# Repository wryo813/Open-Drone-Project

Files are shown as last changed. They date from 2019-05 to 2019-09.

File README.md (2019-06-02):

# Open Drone Project
## 概要
このプロジェクトは、Arduinoプラットフォーム上で開発可能なドローン制御システムの構築を目的としています。
***
# ハードウェア
## 電源仕様
### USBバスパワー給電時
- USB Type-C(USB2.0)で供給を行う
- バッテリーの充電が行われる
- バッテリー給電からUSBバスパワー給電に自動的に切り替わる
- システム全体の消費電流が750mAを超えるとリセッタブルヒューズの抵抗値が上がる
- ESP32-WROOM-32とバッテリー残量IC以外のセンサが起動する
- モーターが回転しないようソフト側で制限をかける
### バッテリー給電時
- 供給能力1000mA 3Cの[リチウムイオン二次電池](http://www.kyohritsu.jp/eclib/OTHER/DATASHEET/BATT/dtp603450phr.pdf)から供給を行う
- モーター含むシステム全体に電力を供給する
- すべての負荷はバッテリー残量ICを通過して電力が供給される
- 全モーターの消費電流が3A(仮)を超えたらソフト側で制限をかける
### バッテリー充電
- バッテリー充電はMCP73831-2ATI/OTを用いて行う
- 最大充電電流はPROG-GND間抵抗5kΩで最大200mAに設定する
#### MCP73831-2ATI/OTの最大充電電流の設定([公式データシート](https://www.microchip.jp/docs/DS21984B_JP.pdf)より)
```
IREG=最大充電電流
PROG=最大充電電流設定用抵抗

IREG=1000[V]/PROG[kΩ]
```
原則`最大充電電流[mA]≦バッテリー容量[mAh]`で設定する
### 消費電力
#### USBバスパワー給電時
|負荷 |消費電流 |
|---|---|
|[ESP32-WROOM-32D](https://www.espressif.com/sites/default/files/documentation/esp32-wroom-32_datasheet_en.pdf)|500mA|
|[MCP73831-2ATI/OT](https://www.microchip.jp/docs/DS21984B_JP.pdf)|200mA|
|[BQ27441-G1](http://www.tij.co.jp/jp/lit/ds/symlink/bq27441-g1.pdf)|0mA|
|[FT231XS](https://www.ftdichip.com/Support/Documents/DataSheets/ICs/DS_FT231X.pdf)|8mA|
|[BMX055](https://ae-bst.resource.bosch.com/media/_tech/media/datasheets/BST-BMX055-DS000.pdf)|8mA|
|[AE-VL53L0X](https://www.st.com/content/ccc/resource/technical/document/datasheet/group3/b2/1e/33/77/c6/92/47/6b/DM00279086/files/DM00279086.pdf/jcr:content/translations/en.DM002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)|19mA|
|[B0067](http://www.arducam.com/downloads/shields/ArduCAM_Mini_2MP_Camera_Shield_DS.pdf)|70mA|
|[モーター](http://www.vibration-motor.com/products/download/Q7AL2BX180003.pdf)|0mA|
|**合計**|805mA|
#### バッテリー給電時
|負荷 |消費電流 |
|---|---|
|[ESP32-WROOM-32D](https://www.espressif.com/sites/default/files/documentation/esp32-wroom-32_datasheet_en.pdf)|500mA|
|[MCP73831-2ATI/OT](https://www.microchip.jp/docs/DS21984B_JP.pdf)|0mA|
|[BQ27441-G1](http://www.tij.co.jp/jp/lit/ds/symlink/bq27441-g1.pdf)|0.097mA|
|[FT231XS](https://www.ftdichip.com/Support/Documents/DataSheets/ICs/DS_FT231X.pdf)|8mA|
|[BMX055](https://ae-bst.resource.bosch.com/media/_tech/media/datasheets/BST-BMX055-DS000.pdf)|8mA|
|[AE-VL53L0X](https://www.st.com/content/ccc/resource/technical/document/datasheet/group3/b2/1e/33/77/c6/92/47/6b/DM00279086/files/DM00279086.pdf/jcr:content/translations/en.DM002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)|19mA|
|[B0067](http://www.arducam.com/downloads/shields/ArduCAM_Mini_2MP_Camera_Shield_DS.pdf)|70mA|
|[モーター](http://www.vibration-motor.com/products/download/Q7AL2BX180003.pdf)|1130.4mA|
|**合計**|1739.097mA|
## 基板仕様
[回路図](https://twitter.com/w_ryo813/status/1123922796239781891)
[基板レイアウト](https://twitter.com/w_ryo813/status/1123887101588774915)
### 基板サイズ
- メイン基板 46×60mm
- 最外サイズ 95×95mm

# ソフトウェア
メインのプログラムは[Drone.ino](https://github.com/wryo813/Open-Drone-Project/blob/master/Drone.ino)
## 通信仕様
- 無線通信はWi-Fiを使って、送信機とドローン本体の一対一で行う
- 送信機とドローン本体は、両方ともAP+STAモードで相互に通信する
- 通信プロトコルはUDPを使用する
- Wi-Fi接続で使用するライブラリは[WiFi.h](https://www.arduino.cc/en/Reference/WiFi)
- UDP通信で使用するライブラリは[WiFiUdp.h](https://github.com/espressif/arduino-esp32/blob/master/libraries/WiFi/src/WiFiUdp.h)
### 送信機から送信するデータ
- 各モーターの目標角度
- YAW軸の目標角速度
- ドローン本体の目標高度
- 緊急停止信号
### ドローン本体から送信するデータ
- バッテリー残量
- 消費電力
- 残り飛行可能時間

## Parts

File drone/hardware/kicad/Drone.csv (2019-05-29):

ID | 参照記号 | パッケージ | 数 | 名称 | Supplier and ref
1 | U7 | Texas_S-PVSON-N10 | 1 | TPS63001
2 | U3 | BMX055 | 1 | BMX055
3 | J6 | JST_ACH_BM02B-ACHSS-GAN-ETF_1x02-1MP_P1.20mm_Vertical | 1 | Motor2
4 | J7 | JST_ACH_BM02B-ACHSS-GAN-ETF_1x02-1MP_P1.20mm_Vertical | 1 | Motor3
5 | J8 | JST_ACH_BM02B-ACHSS-GAN-ETF_1x02-1MP_P1.20mm_Vertical | 1 | Motor4
6 | J5 | JST_ACH_BM02B-ACHSS-GAN-ETF_1x02-1MP_P1.20mm_Vertical | 1 | Motor1
7 | J4 | JST_PH_S8B-PH-SM4-TB_1x08-1MP_P2.00mm_Horizontal | 1 | B0067
8 | J2 | JST_PH_S3B-PH-SM4-TB_1x03-1MP_P2.00mm_Horizontal | 1 | Battery
9 | SW1 | SW_SKRPACE010 | 1 | Power
10 | R41 | R_0603_1608Metric | 1 | 2.2M
11 | R45,R14,R15,R16,R18,R44 | R_0603_1608Metric | 6 | 5.1k
12 | REF**,REF**,REF**,REF** | motor | 4 | motor
13 | R34,R17,R19,R20,R21,R22,R23,R24,R25,R26,R27,R28,R29,R30,R31,R32,R35,R36,R37,R38,R46,R47,R48 | R_0603_1608Metric | 23 | 10k
14 | C1,C2 | C_0603_1608Metric | 2 | 47p
15 | C3 | C_0603_1608Metric | 1 | 0.01μ
16 | C4,C5,C6,C7,C8,C9,C10,C11,C12,C13,C14,C15,C29 | C_0603_1608Metric | 13 | 0.1μ
17 | C16 | C_0603_1608Metric | 1 | 0.47μ
18 | C19 | C_0603_1608Metric | 1 | 1μ
19 | C20,C21,C22 | C_0603_1608Metric | 3 | 4.7μ
20 | C23,C28,C30 | C_0603_1608Metric | 3 | 10μ
21 | C24,C25,C26,C27 | C_1210_3225Metric | 4 | 47μ
22 | D1,D3,D4,D5,D6 | D_SOD-123F | 5 | RB161MM-20
23 | D7 | LED_0603_1608Metric_Castellated | 1 | CHG
24 | D8 | LED_0603_1608Metric_Castellated | 1 | RX
25 | D9 | LED_0603_1608Metric_Castellated | 1 | TX
26 | D10 | LED_0603_1608Metric_Castellated | 1 | Power
27 | F1 | Fuse_1210_3225Metric | 1 | MICROSMD050F-2
28 | J1 | USB_C_Receptacle_Amphenol_12401610E4-2A | 1 | USB_C_Receptacle_USB2.0
29 | J3 | JST_S6B-ZR-SM4A-TF(LF)(SN) | 1 | AE-VL53L0X
30 | L1 | L_0805_2012Metric | 1 | BLM21PG331SN
31 | L2 | INDC2520X100 | 1 | LQM2HPN2R2MJH
32 | Q1,Q2 | SOT-23 | 2 | SS8050-G
33 | Q3,Q4 | SOT-23 | 2 | MMBT3904
34 | Q5 | SOT-23 | 1 | MMBT3906
35 | Q6,Q7,Q8,Q9 | SOT-23 | 4 | IRLML6344
36 | Q11 | SOT-23 | 1 | DMG3415U
37 | R1 | R_1206_3216Metric | 1 | 0.01Ω
38 | R2,R3 | R_0603_1608Metric | 2 | 22
39 | R4,R5,R6,R7,R33 | R_0603_1608Metric | 5 | 47
40 | R8 | R_0603_1608Metric | 1 | 100
41 | R9,R10 | R_0603_1608Metric | 2 | 470
42 | R11,R12,R13 | R_0603_1608Metric | 3 | 1k
43 | R39,R40 | R_0603_1608Metric | 2 | 1M
44 | R42,R43 | R_0603_1608Metric | 2 | 2.7k
45 | SW2 | SW_SKRPACE010 | 1 | EN
46 | SW3 | SW_SKRPACE010 | 1 | Boot
47 | U1 | ESP32-WROOM-32 | 1 | ESP32-WROOM-32D
48 | U2 | SSOP-20_3.9x8.7mm_P0.635mm | 1 | FT231XS
49 | U4 | Texas_S-PDSO-N12 | 1 | BQ27441-G1
50 | U6 | SOT-23-5 | 1 | MCP73831-2-OT

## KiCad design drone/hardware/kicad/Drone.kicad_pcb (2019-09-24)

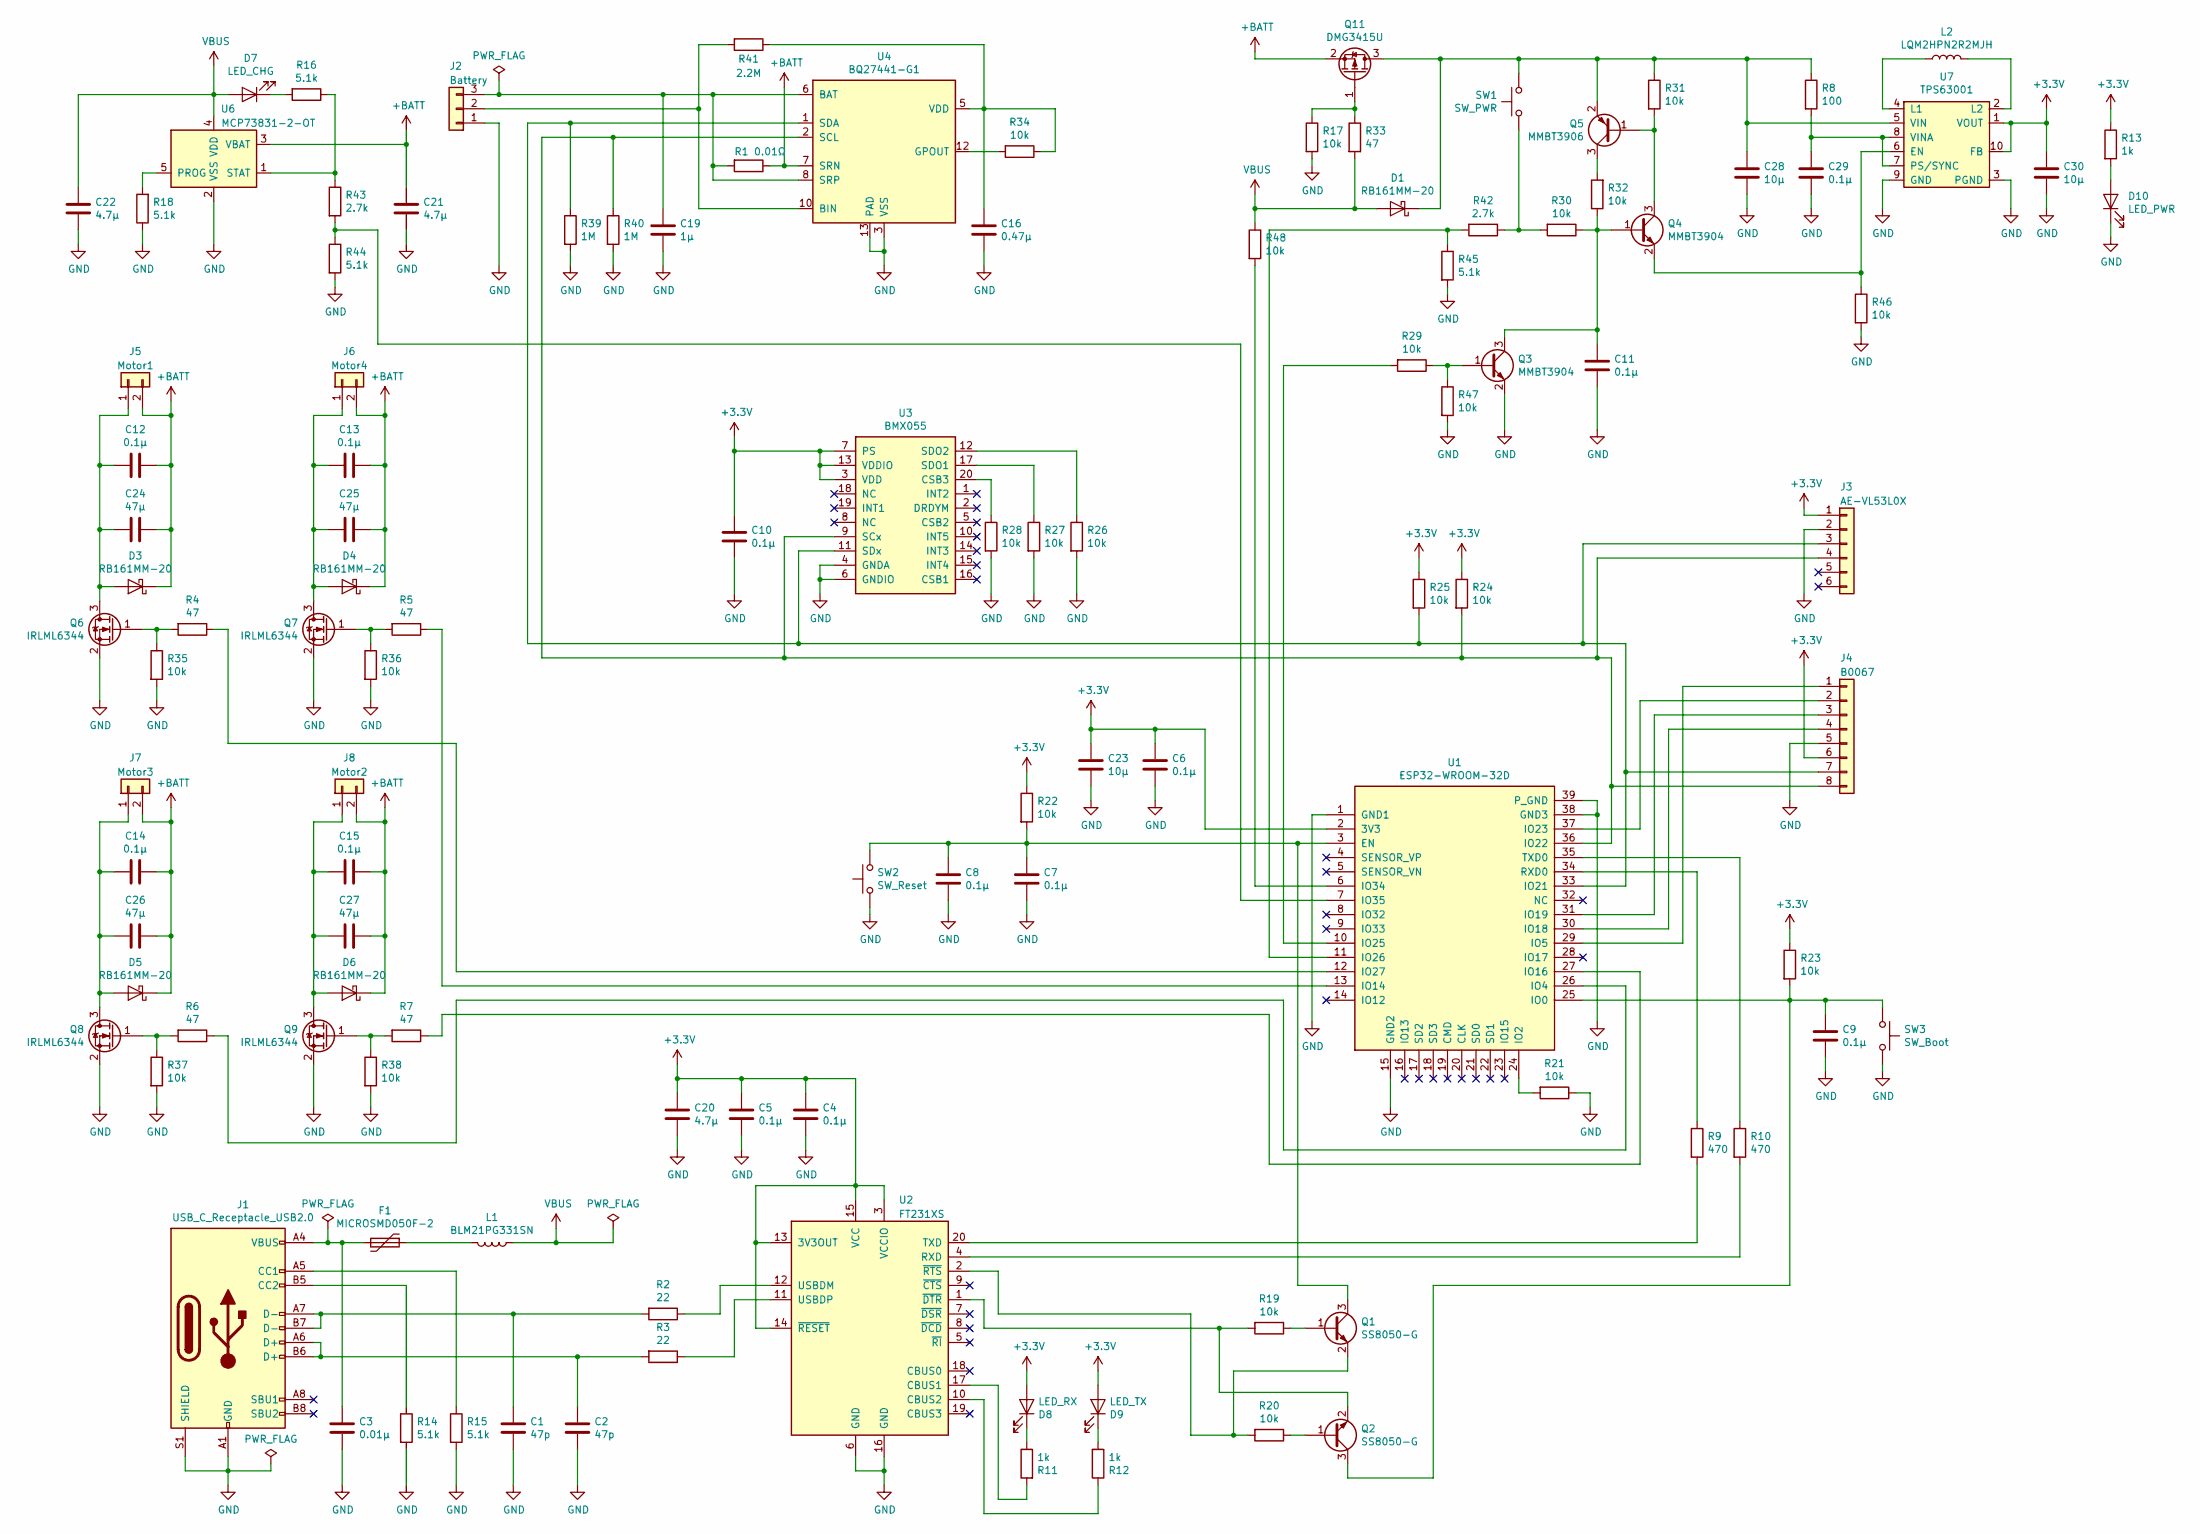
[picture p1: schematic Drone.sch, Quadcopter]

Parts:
C1, C2: 47p; C_0603_1608Metric
C3: 0.01μ; C_0603_1608Metric
C4, C5, C6, C7, C8, C9, C10, C11, C12, C13, C14, C15, C29: 0.1μ; C_0603_1608Metric
C16: 0.47μ; C_0603_1608Metric
C19: 1μ; C_0603_1608Metric
C20, C21, C22: 4.7μ; C_0603_1608Metric
C23, C28, C30: 10μ; C_0603_1608Metric
C24, C25, C26, C27: 47μ; C_1210_3225Metric
D1, D3, D4, D5, D6: RB161MM-20; D_SOD-123F
D7: LED_CHG; LED_0603_1608Metric_Castellated
D8: LED_RX; LED_0603_1608Metric_Castellated
D9: LED_TX; LED_0603_1608Metric_Castellated
D10: LED_PWR; LED_0603_1608Metric_Castellated
F1: MICROSMD050F-2; Fuse_1210_3225Metric
J1: USB_C_Receptacle_USB2.0; USB_C_Receptacle_Amphenol_12401610E4-2A
J2: Battery; JST_PH_S3B-PH-SM4-TB_1x03-1MP_P2.00mm_Horizontal
J3: AE-VL53L0X; JST_S6B-ZR-SM4A-TF(LF)(SN)
J4: B0067; JST_PH_S8B-PH-SM4-TB_1x08-1MP_P2.00mm_Horizontal
J5: Motor1; JST_SHL_SM02B-SHLS-TF_1x02-1MP_P1.00mm_Horizontal
J6: Motor4; JST_SHL_SM02B-SHLS-TF_1x02-1MP_P1.00mm_Horizontal
J7: Motor3; JST_SHL_SM02B-SHLS-TF_1x02-1MP_P1.00mm_Horizontal
J8: Motor2; JST_SHL_SM02B-SHLS-TF_1x02-1MP_P1.00mm_Horizontal
L1: BLM21PG331SN; L_0805_2012Metric
L2: LQM2HPN2R2MJH; INDC2520X100
Q1, Q2: SS8050-G; SOT-23
Q3, Q4: MMBT3904; SOT-23
Q5: MMBT3906; SOT-23
Q6, Q7, Q8, Q9: IRLML6344; SOT-23
Q11: DMG3415U; SOT-23
R1: 0.01Ω; R_1206_3216Metric
R2, R3: 22; R_0603_1608Metric
R4, R5, R6, R7, R33: 47; R_0603_1608Metric
R8: 100; R_0603_1608Metric
R9, R10: 470; R_0603_1608Metric
R11, R12, R13: 1k; R_0603_1608Metric
R14, R15, R16, R18, R44, R45: 5.1k; R_0603_1608Metric
R17, R19, R20, R21, R22, R23, R24, R25, R26, R27, R28, R29, R30, R31, R32, R34, R35, R36, R37, R38, R46, R47, R48: 10k; R_0603_1608Metric
R39, R40: 1M; R_0603_1608Metric
R41: 2.2M; R_0603_1608Metric
R42, R43: 2.7k; R_0603_1608Metric
SW1: SW_PWR; SW_SKRPACE010
SW2: SW_Reset; SW_SKRPACE010
SW3: SW_Boot; SW_SKRPACE010
U1: ESP32-WROOM-32D; ESP32-WROOM-32
U2: FT231XS; SSOP-20_3.9x8.7mm_P0.635mm
U3: BMX055; PQFN50P450X300X100-20N
U4: BQ27441-G1; Texas_S-PDSO-N12
U6: MCP73831-2-OT; SOT-23-5
U7: TPS63001; Texas_S-PVSON-N10

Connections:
+3V3: C4.1, C5.1, C6.1, C10.1, C20.1, C23.1, C30.1, D8.2 (A), D9.2 (A), J3.1, J4.6, R13.1, R22.1, R23.1, R24.1, R25.1, U1.2 (3V3), U2.3 (VCCIO), U2.13 (3V3OUT), U2.14 (~RESET), U2.15 (VCC), U3.3 (VDD), U3.7 (PS), U3.13 (VDDIO), U7.1 (VOUT), U7.10 (FB)
+BATT: C12.1, C13.1, C14.1, C15.1, C21.1, C24.1, C25.1, C26.1, C27.1, D3.1 (K), D4.1 (K), D5.1 (K), D6.1 (K), J5.2, J6.2, J7.2, J8.2, Q11.2 (S), R1.1, U4.7 (SRN), U6.3 (VBAT)
GND: C1.2, C2.2, C3.2, C4.2, C5.2, C6.2, C7.2, C8.2, C9.2, C10.2, C11.2, C16.2, C19.2, C20.2, C21.2, C22.2, C23.2, C28.2, C29.2, C30.2, D10.1 (K), J1.A1 (GND), J1.A12 (GND), J1.B1 (GND), J1.B12 (GND), J1.S1 (SHIELD), J2.1, J3.2, J4.5, Q3.2 (E), Q6.2 (S), Q7.2 (S), Q8.2 (S), Q9.2 (S), R14.2, R15.2, R17.2, R18.1, R21.1, R26.2, R27.2, R28.2, R35.2, R36.2, R37.2, R38.2, R39.2, R40.2, R44.2, R45.2, R46.2, R47.2, SW2.1, SW3.2, U1.1 (GND1), U1.15 (GND2), U1.38 (GND3), U1.39 (P_GND), U2.6 (GND), U2.16 (GND), U3.4 (GNDA), U3.6 (GNDIO), U4.3 (VSS), U4.13 (PAD), U6.2 (VSS), U7.3 (PGND), U7.9 (GND), U7.11
unnamed: C1.1, J1.A7 (D-), J1.B7 (D-), R2.2
unnamed: C2.1, J1.A6 (D+), J1.B6 (D+), R3.2
unnamed: C3.1, F1.2, J1.A4 (VBUS), J1.A9 (VBUS), J1.B4 (VBUS), J1.B9 (VBUS)
unnamed: C7.1, C8.1, Q1.3 (C), R22.2, SW2.2, U1.3 (EN)
unnamed: C9.1, Q2.3 (C), R23.2, SW3.1, U1.25 (IO0)
unnamed: C11.1, Q3.3 (C), Q4.1 (B), R30.1, R32.1
unnamed: C12.2, C24.2, D3.2 (A), J5.1, Q6.3 (D)
unnamed: C13.2, C25.2, D4.2 (A), J6.1, Q7.3 (D)
unnamed: C14.2, C26.2, D5.2 (A), J7.1, Q8.3 (D)
unnamed: C15.2, C27.2, D6.2 (A), J8.1, Q9.3 (D)
unnamed: C16.1, R34.1, R41.1, U4.5 (VDD)
unnamed: C19.1, J2.3, R1.2, U4.6 (BAT), U4.8 (SRP)
unnamed: C28.1, D1.1 (K), Q5.2 (E), Q11.3 (D), R8.1, R31.1, SW1.1, U7.5 (VIN)
unnamed: C29.1, R8.2, U7.7 (PS/SYNC), U7.8 (VINA)
unnamed: D7.1 (K), R16.2
unnamed: D8.1 (K), R11.1
unnamed: D9.1 (K), R12.2
unnamed: D10.2 (A), R13.2
unnamed: F1.1, L1.2
unnamed: J1.A5 (CC1), R15.1
unnamed: J1.B5 (CC2), R14.1
unnamed: J2.2, R41.2, U4.10 (BIN)
unnamed: J3.3, J4.7, R25.2, R39.1, U1.33 (IO21), U3.11 (SDx), U4.1 (SDA)
unnamed: J3.4, J4.8, R24.2, R40.1, U1.36 (IO22), U3.9 (SCx), U4.2 (SCL)
unnamed: J4.1, U1.29 (IO5)
unnamed: J4.2, U1.37 (IO23)
unnamed: J4.3, U1.31 (IO19)
unnamed: J4.4, U1.30 (IO18)
unnamed: L2.1, U7.4 (L1)
unnamed: L2.2, U7.2 (L2)
unnamed: Q1.1 (B), R19.1
unnamed: Q1.2 (E), R20.2, U2.2 (~RTS)
unnamed: Q2.1 (B), R20.1
unnamed: Q2.2 (E), R19.2, U2.1 (~DTR)
unnamed: Q3.1 (B), R29.1, R47.1
unnamed: Q4.2 (E), R46.1, U7.6 (EN)
unnamed: Q4.3 (C), Q5.1 (B), R31.2
unnamed: Q5.3 (C), R32.2
unnamed: Q6.1 (G), R4.2, R35.1
unnamed: Q7.1 (G), R5.2, R36.1
unnamed: Q8.1 (G), R6.2, R37.1
unnamed: Q9.1 (G), R7.2, R38.1
unnamed: Q11.1 (G), R17.1, R33.1
unnamed: R2.1, U2.12 (USBDM)
unnamed: R3.1, U2.11 (USBDP)
unnamed: R4.1, U1.12 (IO27)
unnamed: R5.1, U1.13 (IO14)
unnamed: R6.1, U1.26 (IO4)
unnamed: R7.1, U1.27 (IO16)
unnamed: R9.1, U1.34 (RXD0)
unnamed: R9.2, U2.20 (TXD)
unnamed: R10.1, U1.35 (TXD0)
unnamed: R10.2, U2.4 (RXD)
unnamed: R11.2, U2.17 (CBUS1)
unnamed: R12.1, U2.10 (CBUS2)
unnamed: R16.1, R43.1, U6.1 (STAT)
unnamed: R18.2, U6.5 (PROG)
unnamed: R21.2, U1.24 (IO2)
unnamed: R26.1, U3.12 (SDO2)
unnamed: R27.1, U3.17 (SDO1)
unnamed: R28.1, U3.20 (CSB3)
unnamed: R29.2, U1.10 (IO25)
unnamed: R30.2, R42.1, SW1.2
unnamed: R34.2, U4.12 (GPOUT)
unnamed: R42.2, R45.1, U1.11 (IO26)
unnamed: R43.2, R44.1, U1.7 (IO35)
unnamed: R48.2, U1.6 (IO34)
VBUS: C22.1, D1.2 (A), D7.2 (A), L1.1, R33.2, R48.1, U6.4 (VDD)

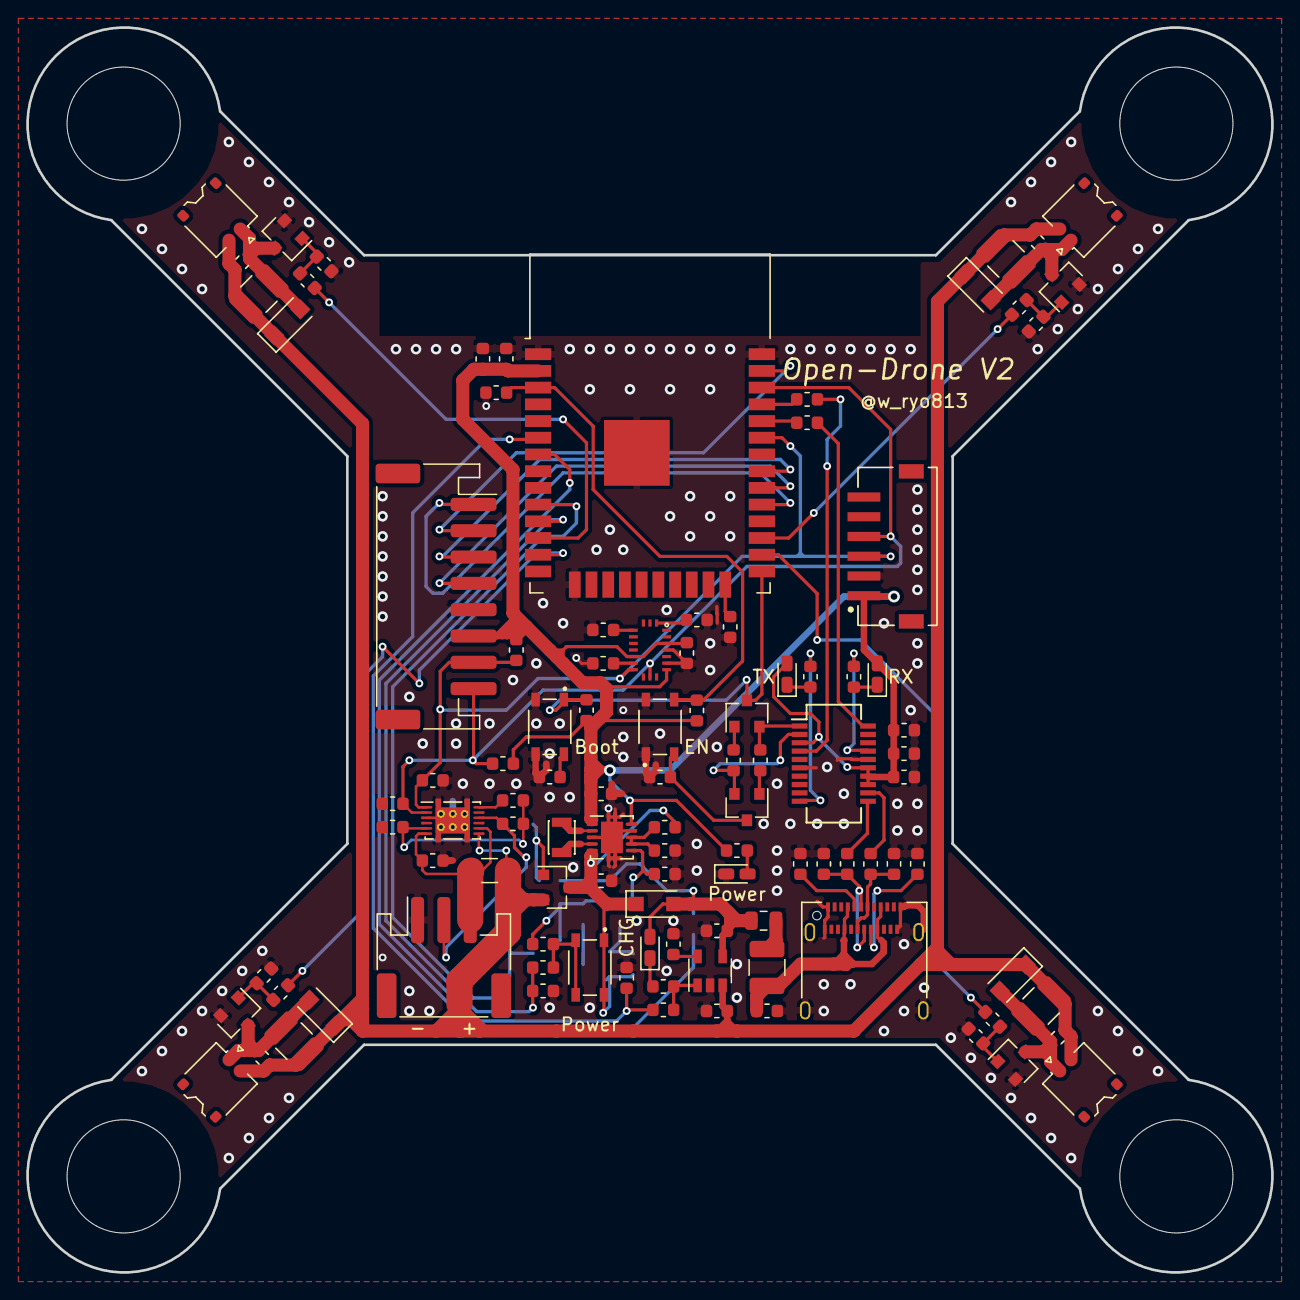
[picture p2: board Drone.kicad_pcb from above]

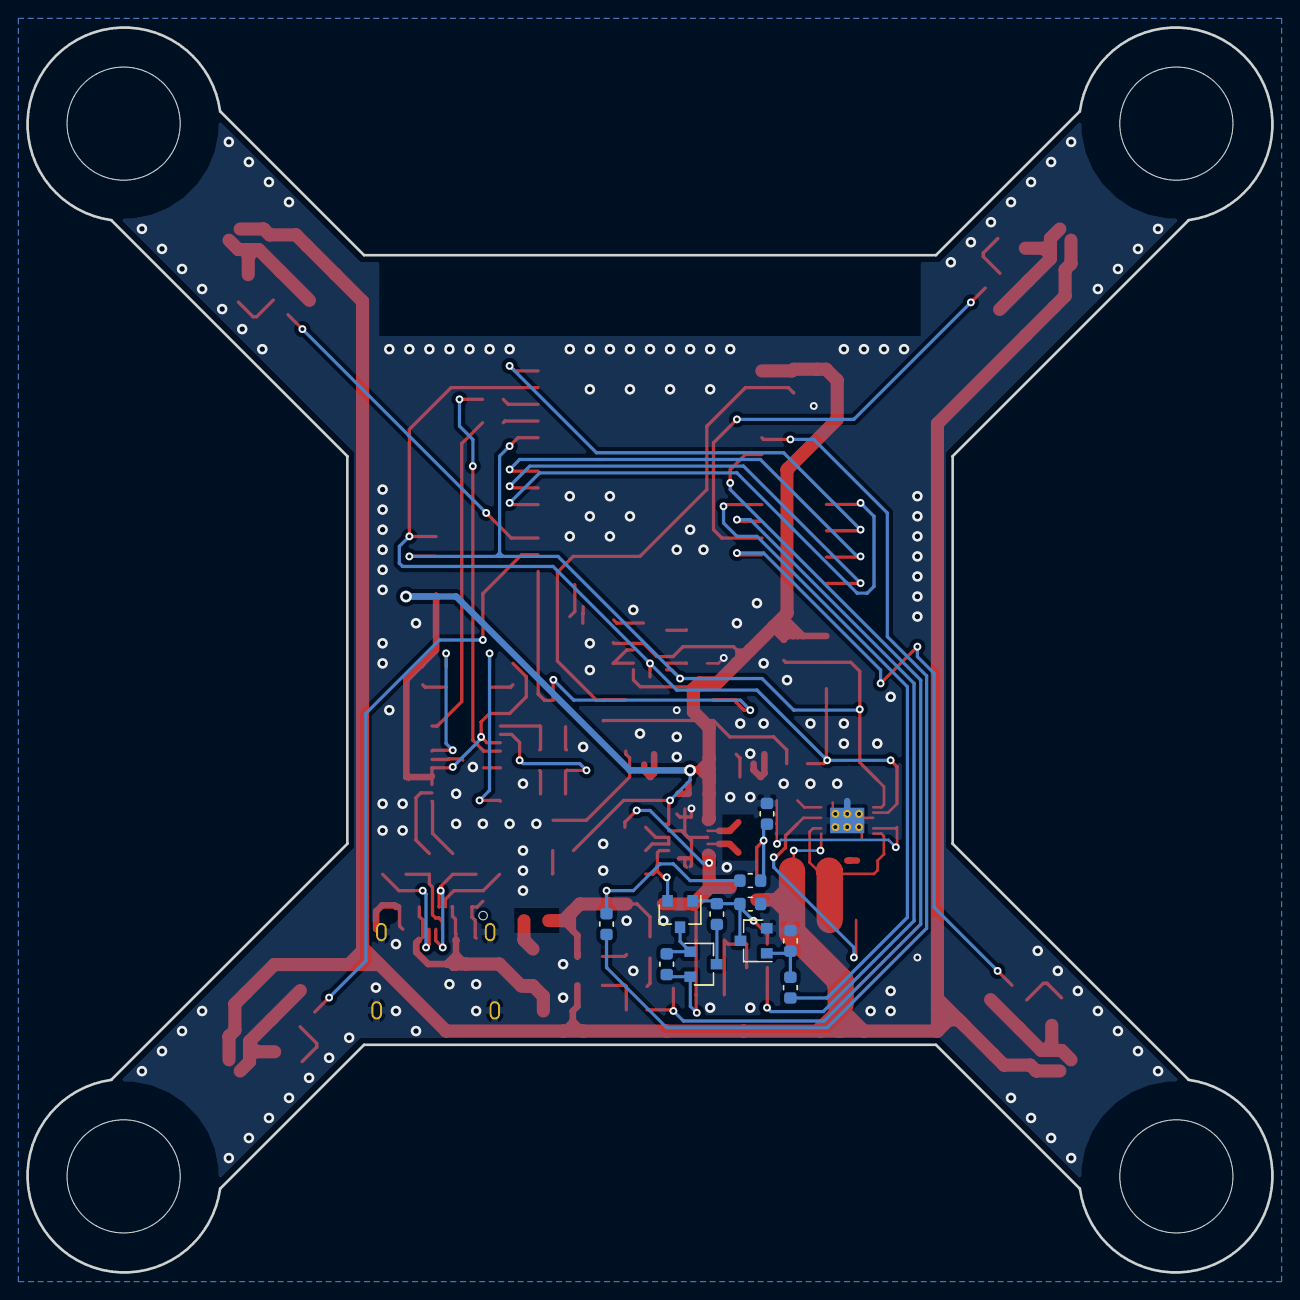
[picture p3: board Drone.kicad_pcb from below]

Board: 2 copper layers, 94.6 x 94.6 mm, 115 parts (11 on the bottom side), 71 nets.

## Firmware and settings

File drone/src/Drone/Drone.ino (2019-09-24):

/*
   メモ
   DTP603450を使ってモータを回転させると3Aでリミッターがかかって供給を停止する
   USB_STATUS_PINを使うとモーターからのノイズでモーターが一時的に停止することがある
   PW_SWITCH_PINを使うとモーターからのノイズで勝手にシャットダウンすることがある
   BQ27441が不安定

   TODO(優先順位)
   高度センサ

   完了
   オイラー角で姿勢角送信
   P_GAINの最適化
   PID制御の実装
   throttle_tgt_rawが0の時のみ電源スイッチを有効にする
   UDP通信で目標姿勢データと起動情報データの分解split関数を使う

   あきらめたこと
   バッテリーステータスの送信（IC割れた）
   電源スイッチ割込み
   カメラの実装
   DTP603450を使うこと
   USB使用時のモーター回転禁止

   PIDパラメータ最適値
   P制御
   P_GAIN=3.80

   PD制御
   P_GAIN=5.80
   D_GAIN=0.60

   PID制御
   P_GAIN 5.80
   I_GAIN 3.70
   D_GAIN 0.87
*/

#include <WiFi.h>
#include <WiFiUDP.h>
#include <MadgwickAHRS.h>
#include <SparkFunBQ27441.h>
#include "GPIO_config.h"
#include "BMX055.h"
#include "split.h"

//バッテリー容量[mAh]
#define BATTERY_CAPACITY 1000

//目標姿勢角度最大値[deg]
#define MAX_POSTURE_ANGLE 40
//目標yaw軸角速度最大値[deg/s]
#define MAX_YAW_VELOCITY 500
//スロットル最大値
#define MAX_THROTTLE 4095

//PIDパラメータ
#define P_GAIN 4.80
#define I_GAIN 2.70
#define D_GAIN 0.87

//yaw軸PIDパラメータ
#define YAW_P_GAIN 0
#define YAW_I_GAIN 0
#define YAW_D_GAIN 0

//重力加速度[m/s^2]
#define G_ACCL 9.80665

//受信する分割文字列数
#define STRING_NUM 6

//アクセスポイント設定 パスワードは8文字以上必要
const char* ssid     = "OpenDroneV2";
const char* password = "ODPpassword";

//自身のIPアドレス
IPAddress ip(192, 168, 4, 1);
//自身のゲートウェイ
IPAddress gateway(192, 168, 4, 1);
//自身のサブネットマスク
IPAddress subnet(255, 255, 255, 0);

//送信先のIPアドレス
static const char *remote_ip = "192.168.4.2";
//自身のUDPポート
static const int local_UDP_port = 8888;
//送信先のUDPポート
static const int rmote_UDP_port = 8889;

WiFiUDP udp;
Madgwick filter;
BMX055 IMU;

void setup() {
  //デバック用シリアル通信は115200bps
  Serial.begin(115200);
  Serial.println("Seial OK");

  //GPIO,PWMの初期化
  GPIO_setup();

  //バッテリー残量IC初期化
  lipo.begin();
  lipo.setCapacity(BATTERY_CAPACITY);
  Serial.println("battery OK");

  //モーションセンサ(BMX055)の初期化
  IMU.begin();
  Serial.println("IMU OK");

  //MadgwickFilterのサンプリンレート[Hz]
  //モーションセンサの出力データレート以下にする25Hz(MAX25Hz)
  filter.begin(25);

  //アクセスポイント構築
  WiFi.softAPConfig(ip, gateway, subnet);
  WiFi.softAP(ssid, password);
  Serial.print("SSID = ");
  Serial.println(ssid);
  Serial.print("Password = ");
  Serial.println(password);
  //機体のIPアドレスを表示
  IPAddress myIP = WiFi.softAPIP();
  Serial.print("AP IP address: ");
  Serial.println(myIP);
  Serial.println("Wi-Fi OK");

  //UDPサーバ構築
  udp.begin(local_UDP_port);
  Serial.println("UDP OK");

  Serial.print("P_GAIN = ");
  Serial.println(P_GAIN);
  Serial.print("I_GAIN = ");
  Serial.println(I_GAIN);
  Serial.print("D_GAIN = ");
  Serial.println(D_GAIN);

  Serial.println("Setting completed");
  delay(300);
}

void loop() {
  //スロットル目標値変数
  unsigned int throttle_tgt = 0;

  //デューティー比生値変数
  int motor1_duty_raw = 0;
  int motor2_duty_raw = 0;
  int motor3_duty_raw = 0;
  int motor4_duty_raw = 0;

  //モーションセンサへ姿勢データ取得リクエスト
  IMU.begin_Accl();
  IMU.begin_Gyro();
  IMU.begin_Mag();
  //モーションセンサから姿勢データを取得
  float gx = IMU.Gyro(x);
  float gy = IMU.Gyro(y);
  float gz = IMU.Gyro(z);
  //加速度センサの生値を重力加速度で割って[G]に変換
  float ax = IMU.Accl(x) / G_ACCL;
  float ay = IMU.Accl(y) / G_ACCL;
  float az = IMU.Accl(z) / G_ACCL;
  float mx = IMU.Mag(x);
  float my = IMU.Mag(y);
  float mz = IMU.Mag(z);

  //モーションセンサ生値をセンサーフュージョン
  filter.update(gx, gy, gz, ax, ay, az, mx, my, mz);
  //Madgwickフィルタで取得した姿勢角度を代入 0≦x＜360[deg]
  float roll  = filter.getRoll();
  float pitch = filter.getPitch();
  float yaw   = filter.getYaw();

  //UDP通信でパケットの存在を確認しサイズをpacketSizeに代入
  int packetSize = udp.parsePacket();
  //もしパケットを受信してたら
  if (packetSize > 0) {
    //UDP通信で受信した文字配列（文字列）を格納する配列
    char packetBuffer[255] = {0};
    //UDP通信での受信したサイズがpacketSizeの文字列をpacketBufferに代入し、受信した文字列の文字数をlenに代入。
    int len = udp.read(packetBuffer, packetSize);
    //分割した文字列を格納する配列をヌル文字で初期化
    String cmds[STRING_NUM] = {"\0"};
    //受信した文字列の最後にヌル文字を追加
    if (len > 0) packetBuffer[len] = '\0';

    //分割数 = 分割処理(文字列, 区切り文字, 配列)
    int index = split(packetBuffer, ',', cmds);
    //UDP到着データ種類判別・破損識別変数
    String data_type = cmds[0];
    //破損識別用最終データ変数
    String end_status = cmds[index - 1];
    //飛行データ取得成功
    if (data_type == "FLIGHT" && end_status == "END") {
      //取得した飛行データを変数に代入
      int roll_tgt_raw     = cmds[1].toInt();//-2047≦x≦2047
      int pitch_tgt_raw    = cmds[2].toInt();//-2047≦x≦2047
      int yaw_vel_tgt_raw  = cmds[3].toInt();//-2047≦x≦2047
      int throttle_tgt_raw = cmds[4].toInt();//0≦x≦4095

      //目標pitch軸角度,roll軸角度,yaw軸角速度の最大値を設定
      float roll_tgt    = (float)roll_tgt_raw    * MAX_POSTURE_ANGLE / 2047;
      float pitch_tgt   = (float)pitch_tgt_raw   * MAX_POSTURE_ANGLE / 2047;
      float yaw_vel_tgt = (float)yaw_vel_tgt_raw * MAX_YAW_VELOCITY  / 2047;
      //スロットル最大値を設定
      throttle_tgt      = throttle_tgt_raw       * MAX_THROTTLE      / 4095;

      //今回yaw軸角速度の算出に使う前回のyaw軸角度を格納する変数
      static float pre_yaw = 0;

      //モーター角度偏差の積分を格納する変数
      static float motor1_intg = 0;
      static float motor2_intg = 0;
      static float motor3_intg = 0;
      static float motor4_intg = 0;
      //yaw軸角速度偏差の積分を格納する変数
      static float yaw_vel_intg = 0;

      //前回のモーター角度偏差を格納する変数
      static float pre_motor1_devi = 0;
      static float pre_motor2_devi = 0;
      static float pre_motor3_devi = 0;
      static float pre_motor4_devi = 0;
      //前回のyaw軸角速度偏差を格納する変数
      static float pre_yaw_val_davi = 0;

      //ループ時間[s]
      float dt = loopTime();

      //yaw軸角速度[deg/s]
      float yaw_vel = (yaw - pre_yaw) / dt;
      //次回のyaw軸角速度算出に使う現在のyaw軸角度
      pre_yaw = yaw;
      //一回転したときに異常な値が出ないようにするための補正
      if (yaw_vel > 600) yaw_vel = yaw_vel - (360 / dt);
      else if (yaw_vel < -600) yaw_vel = yaw_vel + (360 / dt);

      //モーター角度偏差（目標モーター角度と現在のモーター角度の差）
      float motor1_devi = ( roll_tgt + pitch_tgt) - ( roll + pitch);
      float motor2_devi = ( roll_tgt - pitch_tgt) - ( roll - pitch);
      float motor3_devi = (-roll_tgt - pitch_tgt) - (-roll - pitch);
      float motor4_devi = (-roll_tgt + pitch_tgt) - (-roll + pitch);
      //yaw軸角速度偏差（目標yaw軸角速度と現在のyaw軸角速度の差）
      float yaw_vel_davi = yaw_vel_tgt - yaw_vel;

      //モーター角度偏差を時間で積分
      //モーター角度偏差とループ時間[s]をかけた値の累計を算出することで疑似的に積分している
      motor1_intg += motor1_devi * dt;
      motor2_intg += motor2_devi * dt;
      motor3_intg += motor3_devi * dt;
      motor4_intg += motor4_devi * dt;
      //yaw軸角速度偏差を時間で積分
      //yaw軸角速度偏差とループ時間[s]をかけた値の累計を算出することで疑似的に積分している
      yaw_vel_intg += yaw_vel_davi * dt;

      //モーターの暴走防止のため、スロットルが0の時はモーター角度偏差の積分とyaw軸角速度偏差の積分をリセット。
      if (throttle_tgt == 0) {
        motor1_intg = 0;
        motor2_intg = 0;
        motor3_intg = 0;
        motor4_intg = 0;
        yaw_vel_intg = 0;
      }

      //モーター角度偏差を時間で微分
      //モーター角度偏差の変化量をループ時間[s]で割ることで疑似的に微分している
      float motor1_diff = (motor1_devi - pre_motor1_devi) / dt;
      float motor2_diff = (motor2_devi - pre_motor2_devi) / dt;
      float motor3_diff = (motor3_devi - pre_motor3_devi) / dt;
      float motor4_diff = (motor4_devi - pre_motor4_devi) / dt;
      //次回のモーター角度偏差の微分に使う現在のモーター偏差
      pre_motor1_devi = motor1_devi;
      pre_motor2_devi = motor2_devi;
      pre_motor3_devi = motor3_devi;
      pre_motor4_devi = motor4_devi;
      //yaw軸角速度偏差を時間で微分
      //yaw軸角速度偏差の変化量をループ時間[s]で割ることで疑似的に微分している
      float yaw_vel_diff = (yaw_vel_davi - pre_yaw_val_davi) / dt;
      //次回のyaw軸角速度偏差の微分に使う現在のyaw軸角速度偏差
      pre_yaw_val_davi = yaw_vel_davi;

      //yaw軸角速度のPID制御
      float yaw_op = yaw_vel_davi * YAW_P_GAIN +  yaw_vel_intg * YAW_I_GAIN + yaw_vel_diff * YAW_D_GAIN;
      //モーター角度偏差のPID制御
      //yaw軸の制御のため、隣り合うモーターに異符号のyaw軸角速度偏差のPID制御を足す。
      motor1_duty_raw = throttle_tgt + motor1_devi * P_GAIN + motor1_intg * I_GAIN + motor1_diff * D_GAIN + yaw_op;
      motor2_duty_raw = throttle_tgt + motor2_devi * P_GAIN + motor2_intg * I_GAIN + motor2_diff * D_GAIN - yaw_op;
      motor3_duty_raw = throttle_tgt + motor3_devi * P_GAIN + motor3_intg * I_GAIN + motor3_diff * D_GAIN + yaw_op;
      motor4_duty_raw = throttle_tgt + motor4_devi * P_GAIN + motor4_intg * I_GAIN + motor4_diff * D_GAIN - yaw_op;

      //スロットルが0の時はモーターを回転させない
      if (throttle_tgt == 0) {
        motor1_duty_raw = 0;
        motor2_duty_raw = 0;
        motor3_duty_raw = 0;
        motor4_duty_raw = 0;
      }

      //UDP通信で送信するデータを生成
      String send_data  = "STATUS,";
      send_data += (String)millis() + ",";         //起動してからの経過時間
      send_data += (String)pitch_tgt + ",";        //目標pitch角度
      send_data += (String)pitch + ",";            //実測pitch角度
      send_data += (String)lipo.voltage() + ",";   //バッテリー電圧
      send_data += (String)lipo.current(AVG) + ",";//バッテリー電流
      send_data += (String)lipo.soc() + ",";       //バッテリー残量
      send_data += "END";

      //コントローラーにデータを送信
      udp.beginPacket(remote_ip, rmote_UDP_port);
      udp.print(send_data);
      udp.endPacket();
    }
  }

  //モーターのデューティー比を有効な範囲に収める
  motor1_duty_raw = constrain(motor1_duty_raw, 0, 4095);
  motor2_duty_raw = constrain(motor2_duty_raw, 0, 4095);
  motor3_duty_raw = constrain(motor3_duty_raw, 0, 4095);
  motor4_duty_raw = constrain(motor4_duty_raw, 0, 4095);

  //PWMを生成して出力
  //デューティー比は12bit 0≦x≦4095
  ledcWrite(0, motor1_duty_raw);
  ledcWrite(1, motor2_duty_raw);
  ledcWrite(2, motor3_duty_raw);
  ledcWrite(3, motor4_duty_raw);

  //目標スロットルが0かつ電源スイッチが押された時にshutdown_pw()を呼び出す
  if (throttle_tgt == 0 && digitalRead(PW_SWITCH_PIN) == HIGH) {
    shutdown_pw();
  }
}

//電源スイッチが押された時にシャットダウンする関数
void shutdown_pw() {
  //電源スイッチを押し続けている間はシャットダウンしない
  //これがないと、電源スイッチを押し続けている間起動とシャットダウンを繰り返す。
  while (digitalRead(PW_SWITCH_PIN) == HIGH);
  //シャットダウンピンをHIGHにする
  digitalWrite(SHUTDOWN_PIN, HIGH);
}

//ループ時間計測関数
//静的変数を使ってループ時間を計測しているので、二回以上呼び出すと正常に動作しない。
inline float loopTime() {
  float loop_time = 0;
  static float preTime = 0;

  //現在の時間から前回の時間を代入したpreTime引いたものを1000000で割って秒に変換
  loop_time = (micros() - preTime) / 1000000;
  //次の計測に使う現在の時間
  preTime = micros();

  return loop_time;
}

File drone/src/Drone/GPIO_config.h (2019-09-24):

#ifndef GPIO_config_h
#define GPIO_config_h

#include <Arduino.h>

//電源管理ピン設定
#define SHUTDOWN_PIN   25
#define PW_SWITCH_PIN  26
#define USB_STATUS_PIN 34
#define CHG_STATUS_PIN 35

//モーターピン設定
#define MOTOR1_PIN     27
#define MOTOR2_PIN     16
#define MOTOR3_PIN     4
#define MOTOR4_PIN     14

//PWM設定
/*
   PWM周波数とPWM分解能の設定
   T:周期[s],f:周波数[Hz],PWM_BIT:PWM分解能[bit],PWM_FREQ:PWM周波数[Hz] とする
   PWMのクロックタイマの周波数が80MHzの時、PWMのクロックタイマの周期は、
   T=1/f=1/(80×10^6)=12.5×10^(-9)s
   PWMのクロックタイマの周期とPWM分解能をかけた値の逆数がPWM周波数
   f=1/T=1/(12.5×10^(-9)×2^PWM_BIT[bit])=PWM_FREQ[Hz]
*/
//PWM周波数[Hz]
#define PWM_FREQ 19531
//PWM分解能[bit]
#define PWM_BIT 12

//GPIOの設定
void GPIO_setup(){
  //GPIO入出力設定
  //電源関連
  pinMode(PW_SWITCH_PIN, INPUT);
  pinMode(USB_STATUS_PIN, INPUT);
  pinMode(CHG_STATUS_PIN, INPUT);
  pinMode(SHUTDOWN_PIN, OUTPUT);
  //モーターピン
  pinMode(MOTOR1_PIN, OUTPUT);
  pinMode(MOTOR2_PIN, OUTPUT);
  pinMode(MOTOR3_PIN, OUTPUT);
  pinMode(MOTOR4_PIN, OUTPUT);
  //未使用ピン
  pinMode(13, INPUT_PULLUP);
  pinMode(17, INPUT_PULLUP);
  pinMode(32, INPUT_PULLUP);
  pinMode(33, INPUT_PULLUP);

  //モーターピンの初期化
  digitalWrite(MOTOR1_PIN, LOW);
  digitalWrite(MOTOR2_PIN, LOW);
  digitalWrite(MOTOR3_PIN, LOW);
  digitalWrite(MOTOR4_PIN, LOW);

  //PWM設定
  ledcSetup(0, PWM_FREQ, PWM_BIT);
  ledcSetup(1, PWM_FREQ, PWM_BIT);
  ledcSetup(2, PWM_FREQ, PWM_BIT);
  ledcSetup(3, PWM_FREQ, PWM_BIT);

  //ピンをチャンネルに接続
  ledcAttachPin(MOTOR1_PIN, 0);
  ledcAttachPin(MOTOR2_PIN, 1);
  ledcAttachPin(MOTOR3_PIN, 2);
  ledcAttachPin(MOTOR4_PIN, 3);

  Serial.println("GPIO OK");
}

#endif

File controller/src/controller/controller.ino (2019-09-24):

#include <WiFi.h>
#include <WiFiUDP.h>
#include "GPIO_config.h"
#include "split.h"

//ジョイスティックの初期状態の平均値を求める際のジョイスティック電圧読み込み回数
#define AVG_CNT 100

//受信する分割文字列数
#define STRING_NUM 8

//接続先アクセスポイントのSSID/パスワード
const char ssid[] = "OpenDroneV2"; // SSID
const char pass[] = "ODPpassword"; // password

//自身のIPアドレス
IPAddress ip(192, 168, 4, 2);
//自身のゲートウェイ
IPAddress gateway(192, 168, 4, 1);
//自身のサブネットマスク
IPAddress subnet(255, 255, 255, 0);
//自身のDNSサーバ
IPAddress DNS(192, 168, 4, 1);

//送信先のIPアドレス
static const char *remote_ip    = "192.168.4.1";
//自身のUDPポート
static const int local_UDP_port = 8889;
//送信先のUDPポート
static const int rmote_UDP_port = 8888;

//初期状態のジョイスティックの値を格納する変数
int rxv_pro = 0;
int ryv_pro = 0;
int lxv_pro = 0;
int lyv_pro = 0;

WiFiUDP udp;

void setup() {
  //デバック用シリアル通信は115200bps
  Serial.begin(115200);
  
  //GPIOの初期化
  GPIO_setup();
  Serial.println("GPIO OK");
  
  //初期状態のジョイスティックの値を取得
  joystick_proofread();
  Serial.println("Joystick OK");

  //自身のIPアドレス、ゲートウェイ、サブネットマスク、DNSサーバの設定
  WiFi.config(ip, gateway, subnet, DNS);
  //アクセスポイントに設定した機体にWi-Fi接続
  WiFi.begin(ssid, pass);
  Serial.println("weiting");
  //接続されるまで待機
  while (WiFi.status() != WL_CONNECTED);
  Serial.println("conected");
  
  //UDPサーバ構築
  udp.begin(local_UDP_port);
  Serial.println("UDP OK");

  Serial.println("Setting completed");
  delay(300);
}

void loop() {
  //Wi-Fiが切断された時に再接続を開始
  if (WiFi.status() != WL_CONNECTED) {
    //完全にWi-Fiを切断
    WiFi.disconnect();
    delay(50);
    //アクセスポイントに再接続
    WiFi.begin(ssid, pass);
  }
  
  //初期状態のジョイスティックの値を引くことで、ジョイスティックが中心の時に0になる。
  int lxv = analogRead(JOYSTICK_LX_PIN) - lxv_pro;//-2047≦x≦2047
  int lyv = analogRead(JOYSTICK_LY_PIN) - lyv_pro;//0≦x≦4095
  int rxv = analogRead(JOYSTICK_RX_PIN) - rxv_pro;//-2047≦x≦2047
  int ryv = analogRead(JOYSTICK_RY_PIN) - ryv_pro;//-2047≦x≦2047

  //送信する姿勢角度
  //手動でジョイスティックの値を調整
  int roll_tgt_raw     = -ryv - 30;
  int pitch_tgt_raw    =  rxv - 30;
  int yaw_vel_tgt_raw  =  lxv - 30;
  int throttle_tgt_raw =  lyv - 100;
  //throttle_tgt_rawが0よりも小さいときは0を代入
  throttle_tgt_raw = max(throttle_tgt_raw, 0);

  //Mixスイッチがオフの時、姿勢角度とスロットルを0にする(緊急停止)。
  if (digitalRead(MIX_SW_PIN) == LOW) {
    roll_tgt_raw = 0;
    pitch_tgt_raw = 0;
    yaw_vel_tgt_raw = 0;
    throttle_tgt_raw = 0;
  }

  //UDP通信で送信するデータを生成
  String send_data  = "FLIGHT,";
  send_data += (String)roll_tgt_raw + ",";
  send_data += (String)pitch_tgt_raw + ",";
  send_data += (String)yaw_vel_tgt_raw + ",";
  send_data += (String)throttle_tgt_raw + ",";
  send_data += "END";

  //機体にデータを送信
  udp.beginPacket(remote_ip, rmote_UDP_port);
  udp.print(send_data);
  udp.endPacket();

  //UDP通信でパケットの存在を確認しサイズをpacketSizeに代入
  int packetSize = udp.parsePacket(); 
  //もしパケットを受信してたら
  if (packetSize > 0) {
    //UDP通信で受信した文字配列（文字列）を格納する配列
    char packetBuffer[255] = {0};
    //UDP通信での受信したサイズがpacketSizeの文字列をpacketBufferに代入し、受信した文字列の文字数をlenに代入。
    int len = udp.read(packetBuffer, packetSize);
    //分割した文字列を格納する配列をヌル文字で初期化
    String cmds[STRING_NUM] = {"\0"};
    //受信した文字列の最後にヌル文字を追加
    if (len > 0) packetBuffer[len] = '\0';

    //分割数 = 分割処理(文字列, 区切り文字, 配列)
    int index = split(packetBuffer, ',', cmds);
    //UDP到着データ種類判別・破損識別変数
    String data_type = cmds[0];
    //破損識別用最終データ変数
    String end_status = cmds[index - 1];
    //機体データ取得成功
    if (data_type == "STATUS" && end_status == "END") {
      unsigned long time   = cmds[1].toInt();   //機体が起動してからの経過時間
      float recv_pitch_tgt = cmds[2].toFloat(); //目標pitch角度
      float pitch_tgt      = cmds[3].toFloat(); //実測pitch角度
      int battery_voltage  = cmds[4].toInt();   //バッテリー電圧
      int battery_current  = cmds[5].toInt();   //バッテリー電流
      int battery_soc      = cmds[6].toInt();   //バッテリー残量
      Serial.print(time);
      Serial.print(",");
      Serial.print(recv_pitch_tgt);
      Serial.print(",");
      Serial.print(pitch_tgt);
      Serial.print(",");
      Serial.print(battery_voltage );
      Serial.print(",");
      Serial.print(battery_current);
      Serial.print(",");
      Serial.println(battery_soc);
    }
  }
}

//ジョイスティックの初期状態の平均値を求める関数
void joystick_proofread() {
  int rxv_tmp = 0;
  int ryv_tmp = 0;
  int lxv_tmp = 0;
  int lyv_tmp = 0;

  for (int i = 0; i < AVG_CNT; i++) {
    lyv_tmp += analogRead(JOYSTICK_LY_PIN);
  }
  lyv_pro = lyv_tmp / AVG_CNT;

  for (int i = 0; i < AVG_CNT; i++) {
    lxv_tmp += analogRead(JOYSTICK_LX_PIN);
  }
  lxv_pro = lxv_tmp / AVG_CNT;

  for (int i = 0; i < AVG_CNT; i++) {
    rxv_tmp += analogRead(JOYSTICK_RX_PIN);
  }
  rxv_pro = rxv_tmp / AVG_CNT;

  for (int i = 0; i < AVG_CNT; i++) {
    ryv_tmp += analogRead(JOYSTICK_RY_PIN);
  }
  ryv_pro = ryv_tmp / AVG_CNT;
}

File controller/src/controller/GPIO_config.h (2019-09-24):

#ifndef GPIO_config_h
#define GPIO_config_h

#include <Arduino.h>

//ジョイスティックピン設定
#define JOYSTICK_LX_PIN 32 //左ジョイスティックx軸
#define JOYSTICK_LY_PIN 33 //左ジョイスティックy軸
#define JOYSTICK_RX_PIN 34 //右ジョイスティックx軸
#define JOYSTICK_RY_PIN 35 //右ジョイスティックy軸

//スイッチピン設定
#define MIX_SW_PIN      26 //Mixスイッチ
#define GYRO_SW_PIN     25 //5CH Gyroスイッチ

//可変抵抗ピン設定
#define GEAR_PIT_PIN    36 //Gear/Pit可変抵抗

//GPIO設定
void GPIO_setup(){
  //GPIO入出力設定
  //ジョイスティックピン
  pinMode(JOYSTICK_LX_PIN, INPUT);
  pinMode(JOYSTICK_LY_PIN, INPUT);
  pinMode(JOYSTICK_RX_PIN, INPUT);
  pinMode(JOYSTICK_RY_PIN, INPUT);

  //スイッチピン
  pinMode(MIX_SW_PIN,  INPUT);
  pinMode(GYRO_SW_PIN, INPUT);

  //可変抵抗ピン
  pinMode(GEAR_PIT_PIN, INPUT);
  
  Serial.println("GPIO OK");
}

#endif

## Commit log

2019-03-17 デフォルト
2019-03-17 vscodeから
2019-05-06 ジャイロのレンジ変更
2019-05-06 シリアル通信を500000bpsに変更
2019-05-06 Bandwidth 変更
2019-05-10 md変更
2019-05-29 ファイル構成変更
    [Drone.csv, Drone.kicad_pcb, Drone.sch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]
2019-06-02 文字列分割
2019-06-02 文字列分割の高速化
2019-06-07 元バージョン
2019-06-23 電源スイッチ外部割込み動かん
2019-06-23 電源スイッチ外部割り込みやめた
2019-07-06 IMUは動く
2019-07-09 モーターごとに角度を送信
2019-07-13 PD制御を実装
2019-07-20 PID制御の実装
2019-07-28 コメント
2019-07-31 yaw軸PID実装
